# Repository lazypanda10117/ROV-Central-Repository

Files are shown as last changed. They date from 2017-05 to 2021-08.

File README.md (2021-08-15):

## ROV Central Repository

The central repository for 3 underwater Remotely Operated Vehicles (ROV) created for the MATE competition.
They were designed by 3 different engineering teams in AIS between 2015-2017. 
Details about the project and contributors can be found in the corresponding directory.

<br>

**First year of competition - 2015**:

Details of the ROV: [Seagle](Engineering%202015%20-%20Seagle/README.md)

<br>

**Second year of competition - 2016**:

Details of the ROV: [Aquila](Engineering%202016%20-%20Aquila/README.md)

<br>

**Third year of competition - 2017**:

Details of the ROV: [Aquila II](Engineering%202017%20-%20Aquila%20II/README.md)

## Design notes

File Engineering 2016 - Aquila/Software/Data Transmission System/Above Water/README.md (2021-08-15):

# Description of the code

We used the I2C protocol to get the raw data from the under water Arduino to the Arduino above water. Then, we process data and produce human readable information about the current state of the ROV.

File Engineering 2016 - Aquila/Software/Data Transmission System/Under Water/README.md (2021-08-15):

# Description of the code

<br>

**Pressure Sensor**:

The pressure sensor is a relatively small and delicate device, and thus, during the soldering process, it requires definite precision. The pressure sensors after soldering is then waterproofed so that it can be used under water with full exposure. Our system uses an I2C bus communication protocol to interact with the pressure sensor. The data retrieved from the sensor is in mBar (0.1 kilopascal). The main usage of the pressure sensor is to measure the depth of the ROV while under water. Our team has devised an equation for calculating depth based on standard results in fluid mechanics.

<br>

**Temperature Sensor**:

The temperature sensor we have chosen for our ROV is model DS18B20. We deliberately chose DS18B20 as our thermometer because it is waterproof and it uses a unique 1-Wire interface, which requires only one port for communication. The temperature sensor can accurately measures temperatures from –55°C to +125°C (–67°F to +257°F) with only ±0.5°C error.

<br>

**Transmission of data**:

These sensors' data will first be sent to the Arduino under water. Then, it is processed before being sent to the Arduino above water through a CAT-6 ethernet cable. These data will then be displayed on our computer in a custom application we developed using Processing.

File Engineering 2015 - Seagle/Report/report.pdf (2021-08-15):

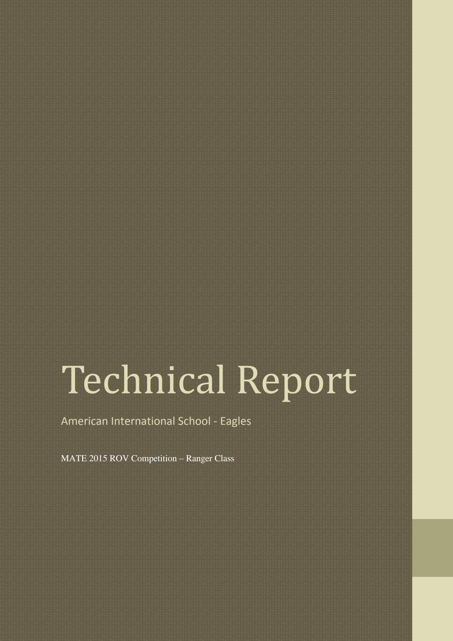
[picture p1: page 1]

# Technical Report

## American International School - Eagles

MATE 2015 ROV Competition – Ranger Class

# Table of Contents:

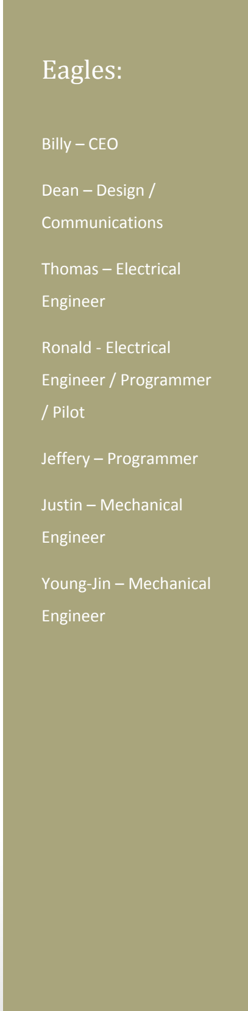
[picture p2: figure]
Technical Report; Eagles:; Billy – CEO; Dean – Design /; Communications; Thomas – Electrical; Engineer; Ronald - Electrical; Engineer / Programmer; / Pilot; Jeffery – Programmer; Justin – Mechanical; Young-Jin – Mechanical

- Introduction
- Rationale for Design:
- Frame
- Propulsion
- Positioning of Thrusters
- Human-Machine Interface
- Camera
- Teamwork
- Safety
- Reflection
- Future Improvements
- Troubleshooting
- Budget
- System Integration Diagram

# Introduction:

Eagles, a young, innovative company dedicated to sea exploration

technology, was formed on August 2014. Eagles is notable for its diligent

employees who worked late nights to engineer their first product – The Fried

Seagle. Its employees are the elites of American International School, who has

been selected through rigorous examinations. Members of the team work on what

they enjoy: coding the human-machine interface program, water-proofing wires,

assembling and positioning the components of ROV. Although seemingly branched

out, all members are knowledgeable and familiar with the product.

- Comment from CEO:

Dream team! Managing and overlooking production for this company is

barely needed. Our employees are knowledgeable, committed, and eager for the

completion of our products. What they do not know will lead their curiosity to

experiment or ask other employees. Eagles provides a welcoming-environment,

where employees are considered family and all opinions are heard and considered.

- Comments from Founder:

I am pleased at the progress our company has made in its first year. The

dedication and determination of our young engineers had been an inspiration to me.

I envision a bright future for this company as employees display their collective

drive and thirst for ocean exploration and technology.

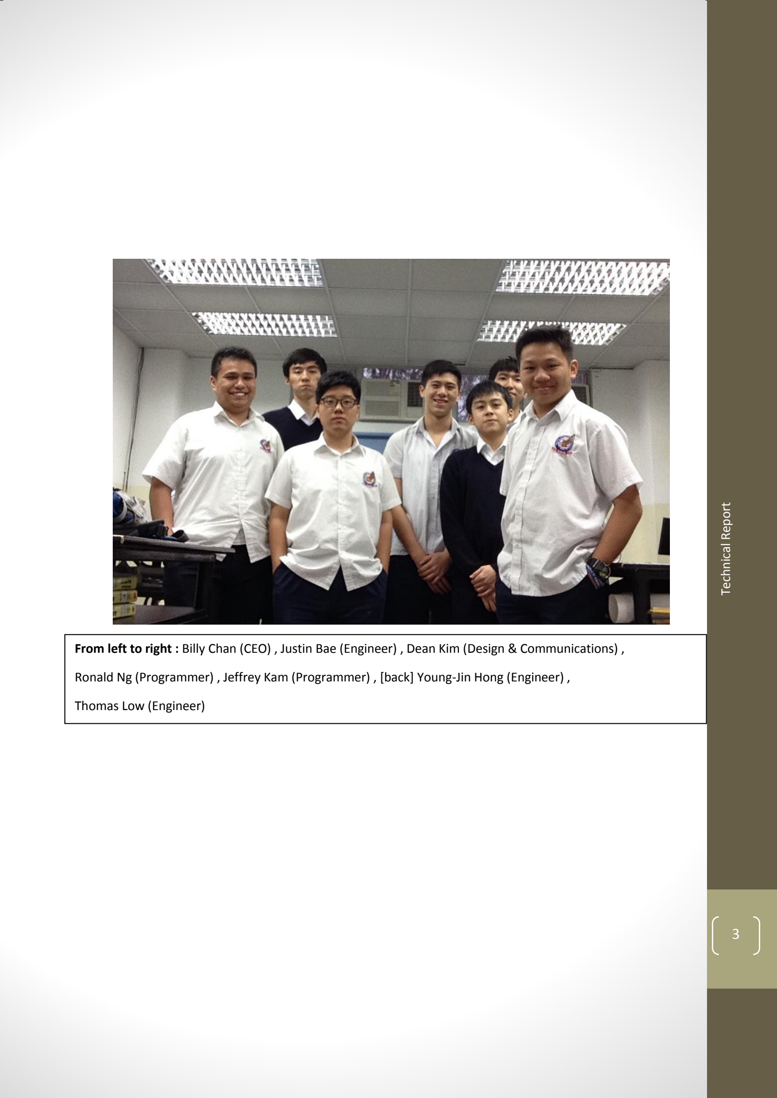
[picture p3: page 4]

Technical Report

3

From left to right : Billy Chan (CEO) , Justin Bae (Engineer) , Dean Kim (Design & Communications) ,

Ronald Ng (Programmer) , Jeffrey Kam (Programmer) , [back] Young-Jin Hong (Engineer) ,

Thomas Low (Engineer)

# Rationale for Design:

- Frame

A cubic frame design has been selected. PVC pipes and joints (L & T) are used

for this particular ROV. There are many advantages of using a PVC pipe. First

of all, the low cost of PVC is definitely and attractive aspect. The light weight

of PVC is another advantage since it ensures unrestrained movement and less

force is required to move the ROV. Durability is also achieved by the cubic

shape as there is no overall weak spot due to the symmetry of the shape. The

design allows easy modification: addition of parts such as lasers, sensors,

cameras, and storage units can be done easily. This model also leaves space

inside the ROV so larger components could be attached inside the cube and

remain protected from collision.

- Propulsion:

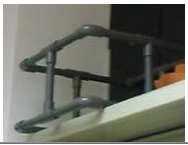
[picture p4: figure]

The ultimate aim for the propulsion system is to provide flexible

underwater movement to the ROV so that it could successfully accomplish

Cubic frame resting on a shelf

5

the missions with great efficiency. Our propulsion system involves six

motors to allow maneuverability in any direction. Motors are made from

bilge pumps, carbon-hydro propellers, and PVC pipes. The large-diameter

PVC pipe is used for shielding. Shielding the propeller is integral to the

performance of the propeller: not only has it prevented cavitation, but also

improved the power of the propeller by minimizing energy loss.

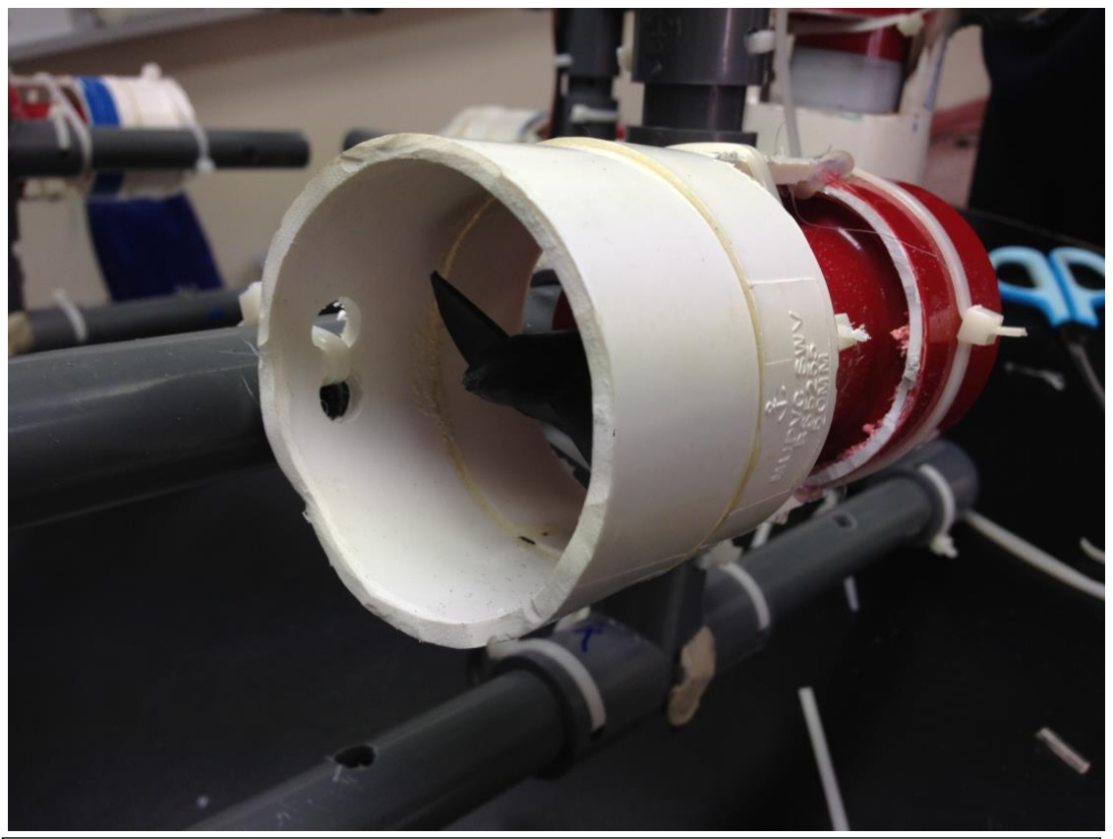
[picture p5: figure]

Positioning of Propulsion

To achieve balanced propulsion for The Fried Seagle, four horizontal

motors are placed symmetrically at each corner of the cubic frame,

relative to where the ROV is facing forward, all in different directions.

One of the motors of The Fried Seagle’s Propulsion system

This positioning allows shifting of the ROV in all horizontal directions

and even provide a vertical motion. Additionally, the positioning provides

a maximum torque when the ROV is performing rotation.

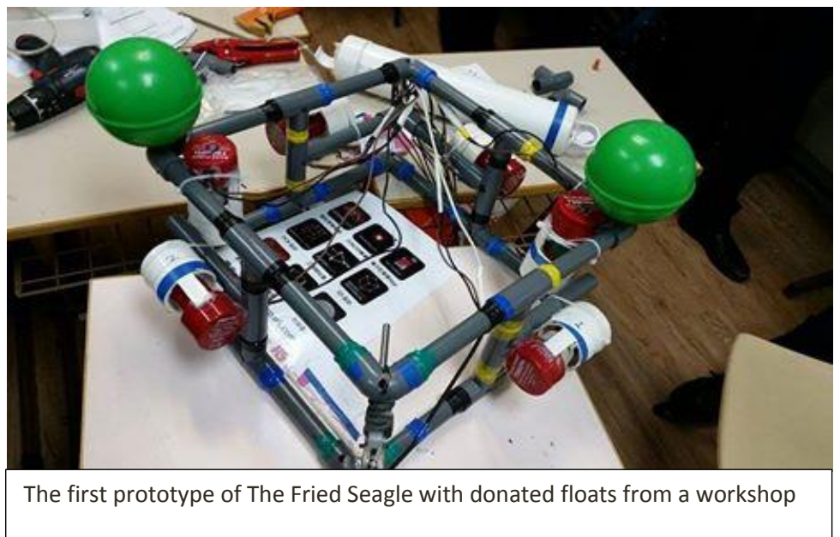
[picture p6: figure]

- Camera:

Seemingly simple to construct, camera plays a vital role in the functioning

of the ROV (after all, clear vision is a must-have for accomplishing any

mission).

The Fried Seagle is equipped with three cameras, frontal camera, down

camera, and full view camera.

- The front camera is the main camera as it shows what is in front of the

ROV. It would be used mainly during inspection missions.

- The down camera is used to identify objects that are under the ROV. As

the ROV is handling tasks underwater, materials might sink and fall to

The first prototype of The Fried Seagle with donated floats from a workshop

7

the bottom. Hence, a down camera could effectively aid in retrieving

any objects sank at the bottom using the hooks.

- Interestingly, the back camera is attached to the wires rather than the

ROV itself. Since it is located above the ROV, it provides a third

perspective to the ROV and hence it can view the surroundings better

and make correct judgements.

All the cameras are based off Spy-Hole B/W Camera K701. These camera

were chosen since they are slim and easily be customizable. Each camera

is inserted into an 11 cm long clear acrylic tube and linked to 5 meter long

cable (directed to a CCTV module, which displays on a portable

computer). It is waterproofing the camera determines the fate of the ROV.

To ensure perfect seal to prevent water from contacting camera and the

soldering inside the tube, 2-part epoxy is used.

- Human-Machine Interface – Programming

Swift Seagle is the program in which human interaction with The Fried Seagle is

made possible. Swift Seagle is composed of sophisticated arithmetic and logical

coding, allowing the Fried Seagle to maneuver at controlled speeds in 3 dimensions

with the input of a PlayStation 2 controller. The swift eagle uses the x and y values

to generate different speeds for each individual motor in order to move in curve

path through various speed. The analog stick of the PS2 controller returns a value

of its x and y value which are between 0 and 255. The way we code the swift eagle

is to think of the x and y values as coordinates, and divide the analog stick into 4

quadrants, like the Cartesian plane, with the x and y values of the analog stick at

stationary point as origin.

9

# Teamwork:

Our company entered the MATE ROV competition for the first time;

therefore, we did not have any experience of engineering a ROV. As we were

constructing the ROV and going through all the trial-and-error, we discovered that

teamwork is the most important aspect. Making this vehicle requires ample

knowledge from various fields: designing, fluid dynamics, mechanical engineering,

computer programming, and material engineering. The robot is the synergy of

those skills and signifies how these skills produce a harmonious spark in

technology. Ronald and Jeffery, who possessed talent and passion for computer

programming, worked on programming the motors. Justin, Young-Jin, Jack worked

on mechanical parts on ROV. Thomas provided us requisites for ROV, including

tools and materials for ROV frame and camera and worked on electrical parts for

ROV. Dean worked on technical report since he acquired an overall knowledge

about ROV. As a president of Engineering Club, Billy managed the team and

allocated our work efficiently and showed us great responsibility to this task. Unite,

we stand – Our team boasted one’s unparalleled strength and each member

contributed to the strenuous task of construction a ROV. We discussed with each

other and shared each other’s ideas. We would seek ways to improve and modify.

The fruit of the hard discussion was a collage of ingenious ideas weaved together.

Without doubt, teamwork was the MVP of our success in the first attempt to

construct an underwater ROV.

# Safety:

Safety of the ROV is one of our primary concerns when we were designing

the ROV. The Fried Seagle has been designed to meet the competition's safety

requirements. The team followed strict safety procedures during the engineering of

the ROV. We ensured that all electric parts must be sealed perfectly to eliminate

gap for water to leak in and cause a short circuit. During our construction of the

ROV, the crew must adhere safety procedures. We ensured that the proper safety

equipment are worn when using specific tools including saws and drill. Propeller

For instance, shields had been used to prevent people from accidents caused by the

blade of the propellers. Each engineer has received training on the correct use of

the tool that were used during construction and every one followed a strict safety

protocol to ensure the highest degree of safety.

11

# Reflection:

Considering the size of our team, insufficient manpower, and lack of time,

our engineering team has gained an ultimate success in completing a full-

functioning ROV. We understand the down-sides of our vehicle, Eagles is proud to

present The Fried Seagle as the first Engineering club at the American International

School, and to represent our great school against others. With flaws, we find

solutions, and with these solutions, we have learnt great lessons on how to deal in

situations. We are looking forward to further develop and burnish our lessons and

knowledge to culminate a more advanced, well-reflected vehicle.

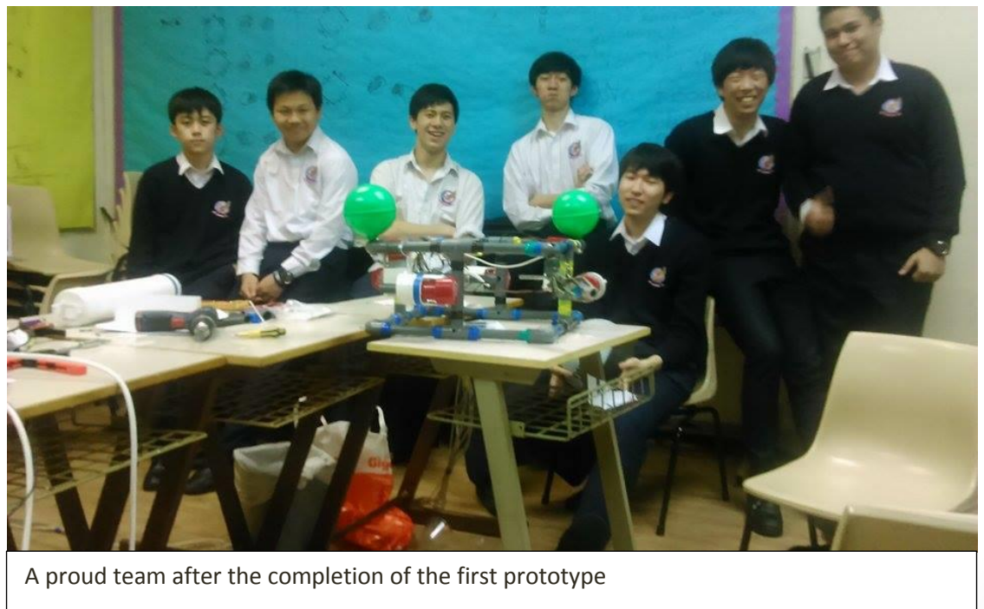
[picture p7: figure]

A proud team after the completion of the first prototype

# Future Improvements:

Since we were novice to constructing ROV, for the first 2 months, our team

worked inefficiently. Having obscure plans for constructing ROV, our club

members did not work efficiently and had to rearrange our frame design a

lot. Every procedure of constructing ROV was a new challenge that almost

everyone had not encountered before; as a result, we constructed our basic Frame

of ROV ineptly, causing re-work of our whole processes. We need to have clear

and detailed plan about ROV construction before we engage the construction. By

doing that we can save more time and consider about our mechanical and

mathematical parts of ROV. We need to calculate actual mechanical physics to

decide with backing proof that our decisions are the best ones. The team’s ambition,

excitement, and impulsiveness has produced a ROV that can and will be even

better.

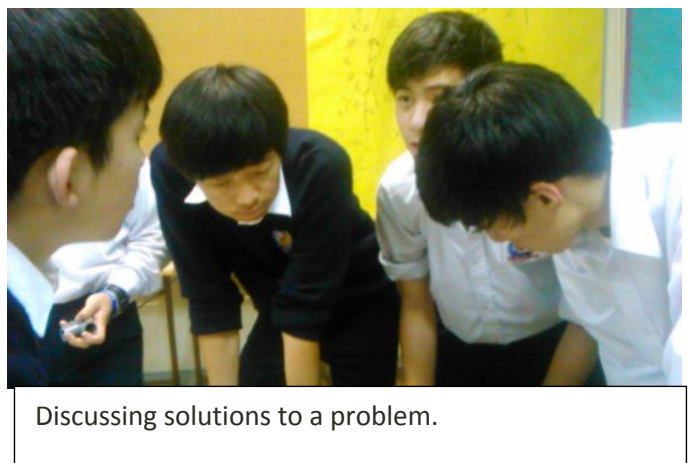
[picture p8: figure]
Discussing solutions to a problem.

13

# Troubleshooting Techniques:

For the efficiency of the work, our company had set up 2 protocols for

troubleshooting. One is used for programming components of the ROV, while the

other manages the mechanical components of the ROV:

- Programming

I

### •Debug the logic of the code by printing out all the output values

II

### - Print the value with a description of what this output means and chec k if it corresponds with the reality

### III

### - check if the pin is working properly

IV

### - draw diagrams on paper to make a thought experiment on how the wi re will be connected and how the code will be executed

V

### - Check the voltage and current passed to the pwm and the voltage and current needed for the motors

VI

### - If doesn’t detect ps2 controller, try adding a 2k resistor for the data wi

re.

# Budget:

As newly-born club, the Engineering Club does not receive a budget from

the school. However, the ambitious members would not allow such a chance to

pass away with the inability to attempt The MATE Competition merely due to a

financial situation.

Starting Budget (Donated from various members of the Eagles company): 3,000 HKD

Item | Quantity | Price per unit | Sub-Total
PVC pipe (2 cm diameter) | 3m | 20HKD/m | 60 HKD
PVC pipe (8.5 cm diameter) | 0.5m | | 10 HKD
PVC cap (for 8.5 cm diameter) | x2 | | 10 HKD
PVC joints (10 L-joints, 8 T-joints) | X18 | | 90 HKD
Two part epoxy | X2 | 270 HKD/set | 540 HKD
Speaker wire | 50m | 30 HKD/5.7m | 263 HKD
Video wire | 12m | 3.5 HKD/0.3m | 140 HKD
Camera | X2 | 280 HKD/unit | 560 HKD
Already water prepared camera | X1 | | DONATED
PWM | X6 | 90 HKD/unit | 540 HKD
Arduino Mega | X1 | 220 HKD/unit | 220 HKD
Arduino Leonardo | X1 | | DONATED
Plastic enclosure | X1 | 75 HKD/unit | 75 HKD
Cable Wire | X3 | 30 HKD/pack | 90 HKD
Sony PlayStation 2 Controller | X1 | 80 HKD/unit | 80 HKD

15

Heat Shrink | ?? | | ~30 HKD
CCTV module | X1 | 398 HKD/unit | 398 HKD
CCTV module-video wire adapter | X4 | 40 HKD/unit | 160 HKD
Male to Male video wire | X4 | 18 HKD/unit | 72 HKD
800GPH Bilge Pump | X3 | 280 HKD/unit | 840 HKD
750GPH Bilge Pump | X3 | | DONATED
Food for workshop | X3 sessions | ~20 HKD/person | ~80 HKD
Tools (Wire stripper, solder, scissors, etc.) | X6 | | 360 HKD

ROV net Total : 2,793 HKD

# System-Integration Diagram: Water

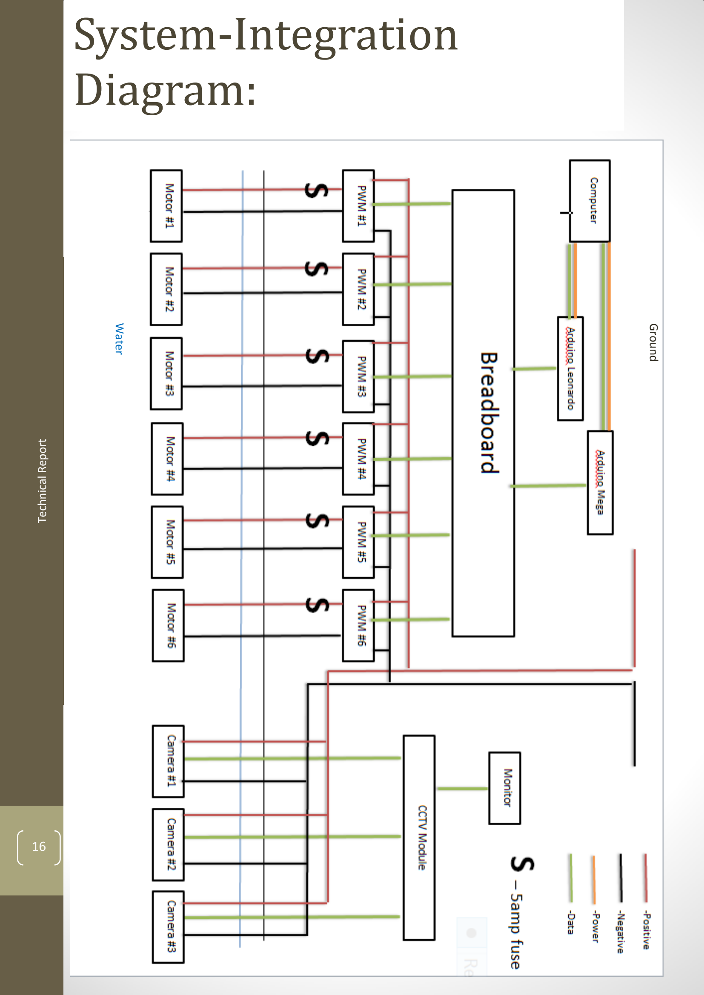
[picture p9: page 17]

Technical Report

16

Ground

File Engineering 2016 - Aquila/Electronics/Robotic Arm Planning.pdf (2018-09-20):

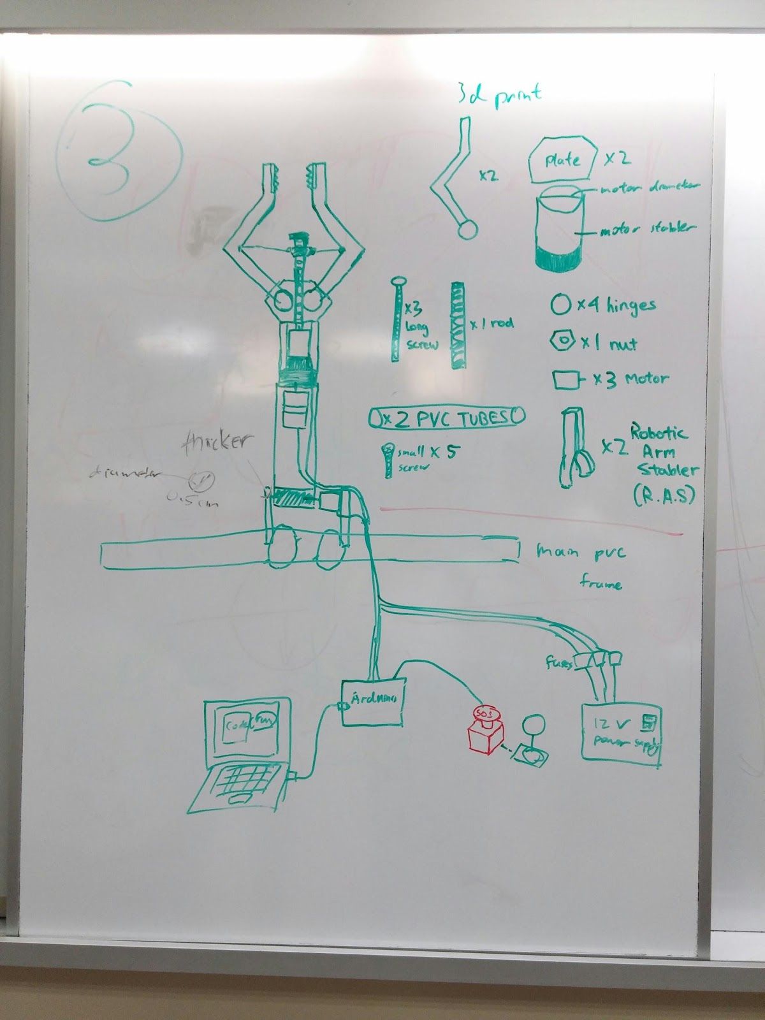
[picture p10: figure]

3D printed parts:
Arm base round as diameter of motor below with 4 hole near the edge and with a distance of the thickness of the jaws on opposite side and a hole in its center
Motor holder, round with a bit larger than the diameter of motor and height of the whole motor + 5 cm

Robotic arm stabler
A small rectangle solid 1.2x3.0 cm with 2 exerted holes on 2 side for insertion of 2 nail
2 square sticks with holes on their ends slightly bigger than the nail size
2 jaws with 2 holes in the end to insert the rod for pivot
2 small rod with diameter of 1 cm with holes on 2 near end with a distance of the thickness of the arm plus the diameter of the screw.
Another motor holder with length of motor length times 2 and cross sectional area of motor diameter + 2 cm and with a 3 cm solid base for inserting a high torque motor to rotate the arm
A round place with 0.5 cm thickness and diameter of previous motor holder and also a little hole in the middle

*all motor holders have 0.5 cm thickness

Non 3d printed parts
6 Brass or bearing
One motor with really high torque
1 motor with medium torque
1 servo
2 plastic soft frictional thing

4 nut for arm linear motion hinge
4 small screw for the hinge also

8 nuts for additional height above the arm base
4 medium long screw
4 nuts for stabling the pivot rod for the jaws

4 screws for connecting the motor holder and arm base

Epoxy glue
3 meter wires
Wire Connecter
2 pwm for 2 motors
Lots of Arduino wires
1 bread board
1 arduino mega or 2 arduino uno
A 4 way joystick
bIg RED BUTTON

http://www.robotoid.com/howto/choosing-a-motor-type.html

Waterproof DC Motor:
http://letsmakerobots.com/content/waterproofing-dc-motor-sugruhttps://www.youtube.com/watch?v=wIcCz5m9LwQ

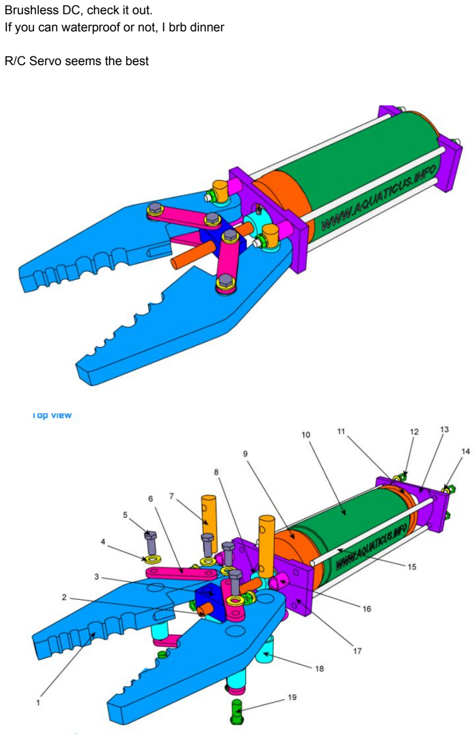
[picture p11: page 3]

Brushless DC, check it out.
If you can waterproof or not, I brb dinner

R/C Servo seems the best

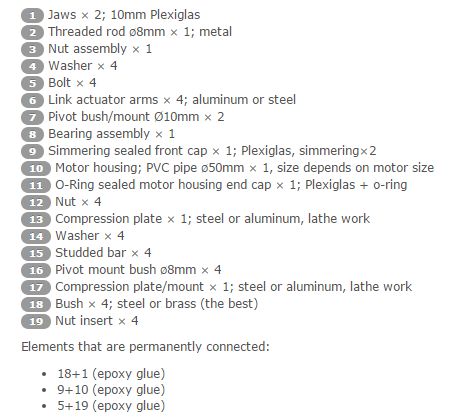
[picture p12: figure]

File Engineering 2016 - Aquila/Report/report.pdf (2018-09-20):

# AQUILA INTEGRADED SOLUTIONS

# american international school hong kong , hong kong

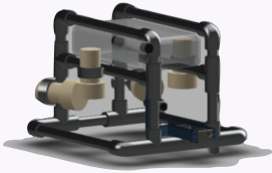
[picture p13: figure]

Billy Chan, Class of 2016
Chief Executive Officer &
Founder

Thomas Low, Class of 2016
Chief of Electrical Engineering

Ronald Ng, Class of 2017
Electrical Engineering

Jamie Fox, Class of 2019
Head of Technical Writing

Tim Chen, Class of 2019
Engineer

Justin Lee, Class of 2019
Engineer

Justin Bae, Class of 2016
Chief of Mechanical Engineering , Project Manger

Jeffery Kam, Class of 2017
Electrical Engineering

Megan So, Class of 2019
Communications Director

Michael Chan, Class of 2019 Engineer

Tony Kovari, Class of 2019 Engineer

Justin Cheung, Class of 2019 Engineer

## The Aquila

### TABLE OF CONTENTS

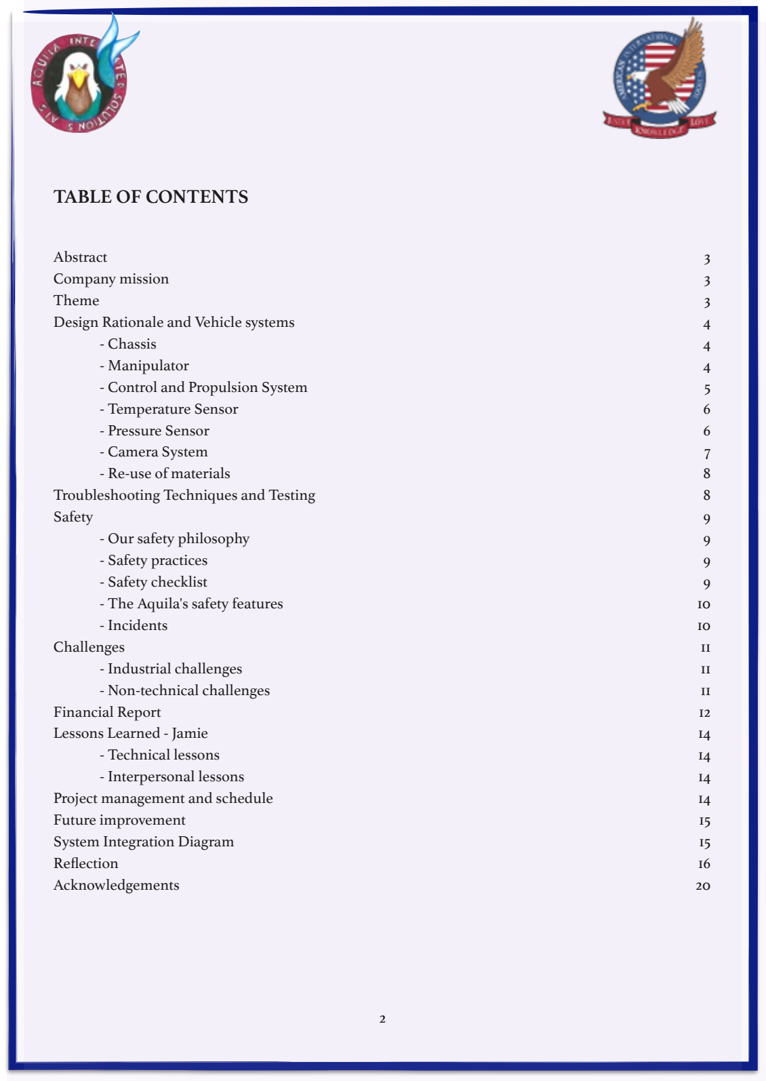
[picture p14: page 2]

Abstract
Company mission
Theme
Design Rationale and Vehicle systems
- Chassis
- Manipulator
- Control and Propulsion System
- Temperature Sensor
- Pressure Sensor
- Camera System
- Re-use of materials
Troubleshooting Techniques and Testing Safety
- Our safety philosophy
- Safety practices
- Safety checklist
- The Aquila's safety features
- Incidents
Challenges
- Industrial challenges
- Non-technical challenges Financial Report
Lessons Learned - Jamie
- Technical lessons
- Interpersonal lessons
Project management and schedule Future improvement
System Integration Diagram Reflection
Acknowledgements

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
Aquila Integrated Systems (AIS) is proud to present its flagship remotely operated vehicle (ROV) product, Aquila. Previously known as Eagles, with new recruits and experience to base our work off of, it was only fitting that the company underwent a name change. From the ashes of The Fried Eagle rises the versatile Aquila. The talented individuals at Aquila Integrated Systems have devised a ROV that is adaptable to the situation presented, adjusting individual modules of the ROV according environmental challenges. Aquila will be equipped with four bilge pump motors (each with propellor shielding), four waterproof cameras, a temperature sensor, a water pressure sensor, and a rotatable mechanical arm. Thanks to the modular design, the company is able to have several mission-critical components created at the same time. With the team coordination from team leader Justin Bae, each module of Aquila does not interfere with another. With its affordability, fixability, and most importantly–adaptivity, Aquila is the ideal ROV for astronautical customers with intent on exploring the depths of oceans in far away worlds.

### ABSTRACT

Aquila Integrated Systems offers practical options through application of different fields of science. This year’s product embodies these fields with our specialized members in mechanical engineering, electrical engineering computer science, and even astronomy (specialized members are enthusiastic or have planned to study in these respective fields when they enter college). AIS seeks innovative solutions to produce awe-inspiring systems with state-of-the-art functionality for our clients.

### COMPANY MISSION

For a company that emerged out of the American International School, it seemed only fitting that the competing ROV team’s name matched the school-wide Eagle theme. The Aquila has an astro-marine focus with the features for effective marine exploration and accessibility and flexibility for the various challenges in space.

### THEME

CHASSIS
The objective design of the chassis was to reduce the amount of material used so that it is easier to control in terms of buoyancy. We decided to use PVC pipes to construct the fundamental shape of the ROV, as we are able to manipulate it very easily and it is strong enough to hold the components of the ROV, but soft enough for us to cut. This gives us a lot of flexibility in terms of changing the dimensions of the ROV. We also drilled holes into the ROV, as it allows the entire chassis to sink. This also makes the buoyancy easier to control and would increase the manoeuvrability of the ROV. We decided to make the Chassis shaped like an upside down pi so that we can input storage space for the ROV’s non-waterproof components. Our design is very minimalistic, as it helps us find any mistakes or broken parts on the ROV very easily. We used PVC pipe glue to secure the parts, as it prevents unnecessary imbalances to how much water is in the chassis. This method is to also add minimum amount of weight to the ROV, making it easier for us to control.

### DESIGN RATIONALE & VEHICLE SYSTEMS

MANIPULATOR
Aquila’s manipulator uses two servo motors; one for opening and closing the jaw, and one for rotation the grip. Since the servos are attached directly to the rotating part, the grip is very durable and free of minor mechanical faults.

Another noteworthy feature of Aquila’s manipulator is that its body is built out of individual aluminium blocks. Hence, we did not have to rely on certain predetermined configuration but were able to easily design and construct the manipulator frame that suits our purposes: First, by using the blocks, we were able to create and attach a platform for the camera on Aquila’s manipulator body. In fact, versatile nature of the blocks allowed us to attach the platform at the ideal location we want. Also, by attaching a PVC pipe joint of the main frame to the manipulator body, we ensured that the manipulator be attached rigidly and naturally to the frame.

CONTROL AND PROPULSION SYSTEM
The control system has a dramatic change from last year’s PS2 design. The control input system includes a Thrustmaster joystick, 2 buttons for up and down movement, and 4 buttons for metallic grip movement; The brain of the control system is 3 arduinos (2 uno and 1 nano); The control output system includes 4 pwm controlling 4 separate motors. The fundamental concept of how the joystick controls the ROV is that the system’s code convert the analog values retrieved from the joystick to x and y values based on the joystick’s center location. Since the analog values received from the joystick are too unstable due to the joystick's sensitivity, the system accounts for the constant varying data first by limiting the maximum and minimum values and then by dividing the each joystick axis into 21 sections, 10 above and to the left of the midpoint section, 10 below and to the right, and one for the equilibrium point. Our team achieve this by mapping the analog value in the constrained range (around 120 to 940) from -10 to 10, and setting 0 as the equilibrium point.

Unlike last year, the xy value is not combining to create a cartesian plane, instead, it separates x as the rotation factor, and y as the linear propulsion factor. For the rotation factor, the system will rotate the ROV in the relative direction of the center of joystick with a speed proportional to the magnitude of the joystick movement. For linear propulsion factor, the ROV will propulse in the y direction of the joystick; simply put, if the joystick location is above half, then it moves forward with magnitude respective to the difference from center, and vice versa for backward. To make the transition from linear propulsion state to rotation state, our team have installed a button that when it is pushed, the system will change to the rotation state and when released, it will return back to linear propulsion state as default. For the z motion (up and down motion), there will be 2 seperate button exclusively for that control as the joystick only provides 2 variables. Our system does not take speed into account for the up and down motion, because usually up and down motion is not a continuous task and does not require as much precisions compared to x and y motion.

The hardware design of the system separates mainly into 2 groups, one for controlling movement, which will be an isolated system that process all the computation above water, and the other for receiving sensors’ data underwater and controlling the arm movement, which transfer data back and forth between an arduino above water and one underwater. There will be 2 different programs in the system, one for reading the joystick analog input and 2 buttons input to control the main ROV movement, and the other for transfer data such as temperature and pressure from the one underwater to the one above water and transfer arm movement input to the one underwater to perform arm motion. The arm itself has 2 servos, one for opening and closing the metallic grip, the other for rotating the whole grip. The second servo is installed due to specific mission. Each servo will have 2 respectives button for controlling, one for each direction for the servo to move. The system also has a safety mechanism that will keep track of the position of the servo so it wouldn't reach the maximum of the degree it can turn and break the servo internally.

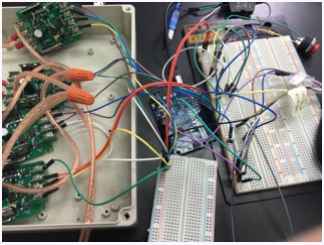
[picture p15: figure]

CAMERA SYSTEM
The Aquila is equipped with four cameras, frontal camera, down camera, and full view camera. The frontal camera is used during missions in inspection missions, and allowing. It also gives use an idea of where we are going. The camera on the arm provides a precise view on the action of the arm, allowing the action to be more precise and making it easier to complete the objective. The down camera is used to help us in locating the object underneath in order to complete the missions, and to locate things that are underneath the ROV. This would help us in obtaining the objects from below. The full view camera is used to provide a birds eye view to the whole pool which allows us to know where everything is in order to plan how to go to each places.

All our cameras are made with Spy-Hole B/W Camera K701. We chose this camera mainly because it is small and easier to be customized. Each camera is put inside a11 cm long clear acrylic tube, linked to 15 meter long cable which is directed to a CCTV module into a computer. We used a 2 part epoxy to seal the camera inside. The reason we chose to use acrylic tube is because it is strong enough to withstand the water pressure, rather than a plastic bottle. Epoxy has the ability to leave no gaps for water to go through into the camera.

The camera systems's power are connected to 4 Underwater Camera Interface circuits. These circuits are capable of transforming 20-9 volts of electricity to 5volts, which the cameras runs on. The circuits consist of one 50v 100μF capacitor, 35v 0.1μF capacitor and a LM7805 voltage regulator. The capacitors are used to prevent damages from the short circuit while the voltage regulator is used to decrease the voltage to 5 volts in order for the camera to use. The circuit is based on a perfboard as it is a lot more flexible during maintenance and debugging. All of the power circuits are enclosed inside a waterproof enclosure with several outlet so that it is completely detachable from the ROV.

Control System Prototype

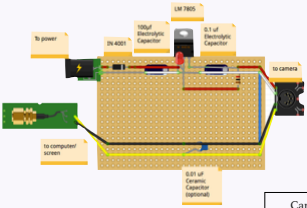
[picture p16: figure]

Camera circuit design

PRESSURE SENSOR
The pressure sensor is a relatively small and delicate device, and thus, during the soldering process, it requires definite precision. The pressure sensors after soldering is then waterproofed so that it can used underwater with full exposure. Our system uses I2C bus communication to interact with the pressure sensors and the data retrieved from the sensors is in mBar, in other words, 0.1 kilopascal. The main usage of the pressure sensor is to measure the depth of the ROV underwater. Our team has devised an equation (int)((pressure*100*1000)-101325)/(0.993*9.8) for calculating depth based on the equation pgh in fluid mechanics. The design of the system is that the pressure sensor will send data to the arduino underwater, then the data is processed into depth through the equation above and then send to the arduino above water through ethernet wire and softwareSerial protocol. The data will then display on the computer's monitor through an application we wrote in Processing, which reads the serial output of the data and display in an organized form on the screen.

TEMPERATURE SENSOR
The temperature sensor we have chosen for our ROV is model DS18B20. We deliberately chose DS18B20 as our thermometer as it’s waterproof and it uses a Unique 1-Wire interface which requires only one port pin for communication. Our temperature sensor can accurately measures temperatures from – 55°C to +125°C (–67°F to +257°F) with only ±0.5°C error.

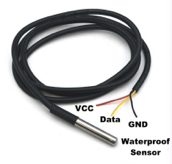
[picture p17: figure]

Diagram of sensor

RE-USE OF MATERIALS
Aquila Integrated Systems salvages and re-uses previous products (The Fried Eagle) solely for tests. With the upbringing of new and sometimes unconventional ideas, it is a certainty that members will have failed to account for errors, even after validation of the new system’s and calculations. Prioritizing safety of the members, re-used materials such as motors, floats, and PWM have been worn-out, experienced leakage, and overheated to the point of flame ignition (respectively). This use of the obsolete items ensures complete development of our solutions, having tested and accounted for all factors (particularly any extraneous aspects that may affect operational performance), as well as test reliability of the system.

All materials that make the Aquila were never of The Fried Eagle. Parts with improved specifications are required for our company’s progressing advancement of our solutions, thus our annual acquisition of brand-new materials is a testament to the company’s growth.

### TROUBLESHOOTING TECHNIQUES AND TESTING

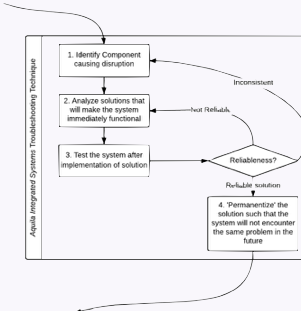
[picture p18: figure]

Safety Philosophy
Safety in using the ROV is one of our primary concern when we were designing the ROV. The Aquila has been designed to meet the competition's safety requirements. No safety issue is too small for us. We employ this philosophy to our design and working habit. After multiple check and test, we have determined that our product meets all the safety standards of IET.

### SAFETY

Safety Practices
The team follows strict safety procedures when the ROV is being constructed. We ensured that all electric parts cannot not have any gap for water to leak in and cause a short circuit. During our construction of the ROV, the crew must follow safety procedures. We ensured that the proper safety equipments are worn when using specific tools including saws and drill. Each engineer has received training on the correct use of the tool that were used during construction and every one followed a

Safety Check

Safety Checklist at Work | Check

Long Hair is tied back

Gloves are worn when handling eproxy

Hearing protection and safety goggles are worn when operating power tools and motor circuits

Clear workstation completely after work

Unplug soldering iron after use

Never touch the metal section of the soldering iron, regardless circumstances

Safety Checklist before Operating the Aquila | Check

All wires are securely connected to ROV

Both ends of the tether are properly lugged in.

Run system check (include motors, cameras sensors)

ROV is securely connected to 12V DC battery.

Safety Checklist when Operating the Aquila | Check

All staff around the pool are aware of the deployment off the ROV

Only one member can act as pilot

No member is allowed to touch the water pool when ROV is in operation.

The Aquila's Safety Features
- Motor Shields has been used to prevent people from accidents caused by the blade of the propellers.
- The tether is tightly secured
- All sharp edges smoothened.
- 25A fuse on main power source.
- Each motor is fitted with a 5A fuse.
- The ROV is also designed to be light which would reduce the force and momentum during a collusion.
- Labels are tagged on wires to prevent users to connect device in the wrong polarity.
- yellow and black safety warning color indicators on motors and other hazardous items
- One camera is tied to the tether for full view of the ROV and its surroundings.

Incidents
Despite the fact that we have taken every single safety, there were still several incident during the development of our ROV. One of notable incident during the development of the ROV took place during the production of the motor control. The PWM circuit for our motor caught on fire during use. We have replaced the PWM circuits with a different model and we included wearing safety protection as one of the protocols when operating the motor circuits just in case. There was another incident when one of our member's hand was injured by a hot soldering iron. After this incident, we especially designed to items on the checklist concerning soldering irons to decrease the possibility of similar accident.

NON-TECHNICAL CHALLENGES
As a novice team, the main problems of the team stemmed from the fact that majority of the teammates were new to the team. Our progress was therefore often heavily reliant to few senior members and resulted in inefficient teamwork

Failing to sufficiently familiarize new members to our project also led to overall lack of motivation. Since many of the members were not fully aware of the necessary concepts or skills, their participation was often very limited.

Lack of organization was also a huge problem that emerged in this context. At the beginning, our team divided ourselves to several sub groups and assigned different tasks to each group. However, as each groups began to encounter more and more problems, the independent nature of each groups resulted in inefficient troubleshooting process that had to be coped only within the group.

### CHALLENGES

TECHNICAL CHALLENGES

One of the main sources of our technical problems came from the Arduino. Failing to accurately wiring the PWM boards and the motors often burnt the Arduino, and members had to make unplanned expenditure in purchasing new sets of Arduino. After several trial and errors, we were finally able to solidify the connections.
Using a joystick to control the motors entailed several problems as well. First, the Arduino code didn’t receive any signal from the joystick if the joystick lever was not tilted perfectly toward 90 degrees angle. This problem prevented us from manipulating the vehicle swiftly and smoothly, since it was it was impossible for us to tilt the lever toward precise right angles continuously.

Unwanted penetration of liquid was another major hindrance. First of all, careless waterproofing often led to fault in our cameras, buoyancy, and especially the robotic arm (the Arduino and other electric boards for the arm are enclosed in the watertight case that submerges underwater with the vehicle).

Budget and Expense Sheet

TYPE | ITEM | UNITS PURCHASED | UNIT PRICE (HKD) | UNIT PRICE (USD) | AMOUNT PRICE (USD)
Frame Section | PVC Pipe (2 metres) | One | $89 .00 | $11.47 | $11.47
Frame Section | Buoyancy Toilet Float | Two | $5.00 | $0.64 | $1.28
Frame Section | Watertight Electronics Enclosure | One | $299.00 | $38.54 | $38.54
Frame Section | PVC Glue | One | $5.00 | $0.64 | $0.64
Propulsion | Blige Pump Motors | Four | $150.00 | $19.34 | $77.36
Propulsion | Propeller | Four | $40.00 | $5.16 | $20.64
Propulsion | Propeller Adapter | Four | $80.00 | $10.31 | $41.24
Propulsion | Propeller Shield* | One | $49.50 | $6.38 | $6.38
Control System | Arduino Nano | Two | $89.00 | $11.47 | $22.94
Control System | Arduino Uno | One | $125.00 | $16.11 | $16.11
Control System | Joystick | One | $265.00 | $34.16 | $34.16
Camera | Rear View Camera (Automobile)* | Four | $206.00 | $26.55 | $79.65
Camera | Power Supply Circuit | Four | $35.00 | $4.51 | $18.04
Camera | Camera Circuit Enclosure | One | $110.00 | $14.18 | $14.18
Camera | Underwater Cable for Camera System | One | $158.00 | $20.37 | $20.37
Camera | Analog to Digital Video Signal Converter | One | $200.00 | $25.78 | $25.78
Camera | Four Channel CCTV Splitter | One | $497.00 | $64.07 | $64.07
Sensor | Digital Temperature Sensor | One | $35.00 | $4.51 | $4.51
Sensor | Pressure Sensor | One | $235.00 | $30.29 | $30.29
Sensor | Underwater Cable for Sensor System | One | $200.00 | $25.78 | $25.78
Arm | Servos | One | $241.00 | $31.07 | $31.07
Arm | Mechanical Claw | One | $123.00 | $15.86 | $15.86
Tools & Equipment | Drenal Drill | One | $1099.00 | $141.67 | $141.67
Tools & Equipment | Water Tank | One | $200.00 | $25.78 | $25.78
Tools & Equipment | Tool Box | Two | $150.00 | $19.34 | $38.68

### FINANCIAL REPORT

* signifies a donation

Expense | Amount in HKD Amount in USD
Frame Section | $402.70 | $51.93
Propulsion | $1129.20 | $145.62
Control System | $567.70 | $73.21
Camera | $1722.10 | $222.10
Sensor | $469.80 | $60.58
Arm | $363.90 | $46.93
Tools and Equipment | $1598.4 | $206.13
Travel Expenses | $300.00 | $38.69

### FINANCIAL REPORT

Total Cost: | $6,553.80 HKD | $845.19 USD

TECHNICAL LESSONS
Learning from our challenges and mistakes while building the Aquila, we have learnt to always have extra arduino boards incase of incidents where the arduino is burnt or is failing to work. Junior members have learnt our team leaders how to code, work the sensors, and developing the design. We have also developed a stronger, more efficient design that been developed by learning from our mistakes in the previous year’s design.

### LESSONS LEARNED

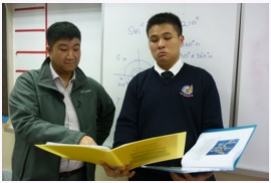
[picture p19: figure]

Mr. Kang and Billy Chan working on concept of ROV

### LESSONS LEARNED

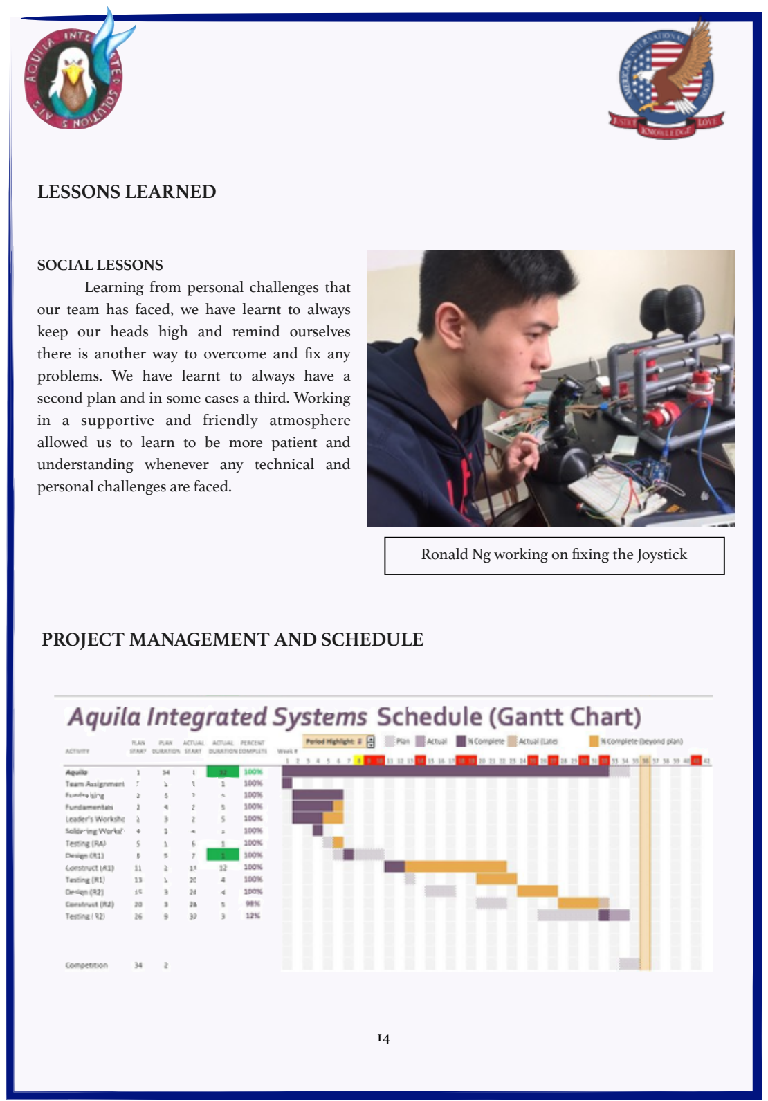
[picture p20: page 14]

SOCIAL LESSONS
Learning from personal challenges that our team has faced, we have learnt to always keep our heads high and remind ourselves there is another way to overcome and fix any problems. We have learnt to always have a second plan and in some cases a third. Working in a supportive and friendly atmosphere allowed us to learn to be more patient and understanding whenever any technical and personal challenges are faced.

### PROJECT MANAGEMENT AND SCHEDULE

Ronald Ng working on fixing the Joystick

Two major areas that need improvements for our team are the following: Lack of passion and Lack of sessions. First of all, due to general incompetence of the members, our teammates frequently experienced limitation to their participation, which eventually led to low motivation. This unpleasant cycle went on and on and lingered as a main source of general inefficiency and low productivity. Starting next year, with more passion and enthusiasm, we believe that our members will be able to participate to their full potential and reach fruitful outcome with our Aquila. In regards to this fact, it is imperative that our members first become competent engineers and gain sufficient knowledge and skill to participate. The problem of this year was that lack of available sessions hindered the progress of our learning. Hence, in order to boost up the passion of the members in the future and expect improvements, Aquila’s crews must first acquire sufficient time to hone their skills and contribute to their full potential.

### FUTURE IMPROVEMENTS

### SYSTEM INTEGERATION DIAGRAM

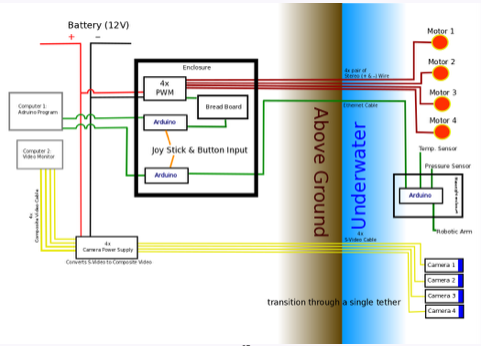
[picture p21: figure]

### REFLECTIONS

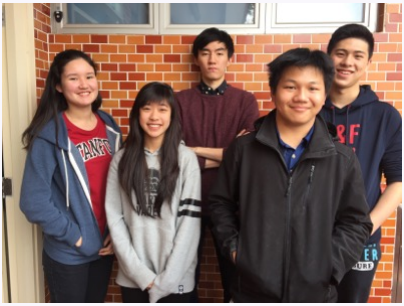
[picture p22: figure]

Justin Bae, Class of 2016
Although our team gathered and prepared for this competition as members of mere school extracurricular club, for me, it was a great opportunity to participate in an activity that I genuinely enjoyed. This competition gave me other several benefits. First of all, my experiences served as an excellent opportunity for me to apply the academic concepts, especially in Physics and Computer Science. By applying into tangible situations and objects, I was able to understand the concepts more clearly and easily, by which I even found chance to achieve pleasant outcomes for my academic endeavors as well. Also, as a team leader, my efforts in the club even allowed me to find opportunity to strengthen my capacity as a leader, through teamwork, resolving conflicts, and organizing the community. In the end, I regard my experiences preparing for this competition as a huge boon throughout my high school years and hope my fellow teammates to find pleasant benefits from this experience as well.

Members of ROV Team
Back Row (left to right): Jamie Fox, Justin Bae, Ronald Ng Front Row (left to right): Megan So, Thomas Low Missing Members: Tony Kovari, Justin Lee, Justin Cheung, Tim Chen, Jeffery Kam

Thomas Low, Class of 2016

This year is the second year I participate in the project. It is a great pleasure work with some old teammates. It is also great to see some new members participating in this project. As I am already familiar with the project I have helped my teammates to start training the new members in advance. I am currently leading the team of freshmen to build the camera system. I particularly enjoy the process of debugging the circuits. I am glad that I am able to use my knowledge from physics and maths to this project. By doing actual application, I am able to understand the subject more. Leading a team of freshmen also helped me on my communication and leadership skills. My experience working in this project has been a great part of my high school life, and I hope my teammates are benefit by this project the same way as I did.

### REFLECTIONS

Jeffrey Kam, Class of 2017

The two core values of engineering for me are exploration and problem solving. During the course of the ROV making process, I have enriched myself in those 2 values. I always try to explore new and more efficient solutions to the existing system, trying to improve it with better code and higher efficiency design. For example, from researching online, I realized that ethernet wire at CAT6 has really low resistance, and thus useful for our design for transferring data between underwater and on ground arduinos. This year, I also have to teach some of the freshmen how to integrate hardware into arduino and write a program that works perfectly uninspected. This new experience allows me to be a better communicator as i always keeps the idea and thinking process to myself and often explain concepts in an overcomplicated way. As one of the main programmer and electronics engineer in the club, I wish train some of the members on the team to have individual problem solving abilities and the heart to explore so in the future after i left, those will be able to make the team thrive with their ability to problem solve and guide the team to explore for new solutions.

Tony Kovari, Class of 2019

This is the first year I worked on any ROV and I learned a lot from the experience juniors and seniors in our team. We are very fortunate to have a great team leader that can motivate people to work and allow time for new members to get a look and feel of the work process. The designs and code made by our senior members benefited the team greatly, without them perhaps we would be behind schedule more than last year.

Tim Chen , Class of 2019

This is my first year in high school and the ROV team, so there were and still are a lot of things I don’t know. But throughout this year, I have learnt more and more on engineering in general from the seniors and juniors in the team. I am currently working on the pressure sensor with a fellow freshman; it isn't an easy job for us since we had no experience with engineering or arduino coding. But with the help from our teacher Mr Kang and other seniors/juniors, we had successfully made a working underwater pressure sensor. During this experience, I had enhanced my problem solving skills as well as my cooperation skills. I look forward to learn more and do more to help our ROV team in the future.

Michael Chan, Class of 2019

During the course of this club, i have learnt a lot about engineering. This was my exposure to engineering, so I had no knowledge that I can apply to this club. I have learnt a lot about arduino and also where to get tools to use. One major contribution I gave was the temperature sensor. First, we had to make sure the sensor was waterproofed. Then, we had to overcome a lot of bugs that prevented the code from working. After successfully running the code, it still did not show the temperature. With the help of seniors, juniors and the teacher, I have successfully made my first working physical product along with a working code.

Justin Lee, Class of 2019

After almost a year of being in engineering club, I have learnt a lot about engineering in general. This club was my first approach to learn about engineering. Throughout this year, I have learned how a ROV works and the safety precautions we have to take while engineering. My contribution to this ROV is working on the temperature sensor. With the help of a very advanced programmer and a teacher, I have successfully made a working temperature sensor with another freshman who also had no experience in programming programming. I look forward to seeing what I will able to accomplish next year with the knowledge I have.

### REFLECTIONS

### REFLECTIONS

Jamie Fox, Class of 2019

As a freshman in High School this year, I had set a goal to myself this year to learn and experience a range of clubs and teams that would help broaden my learning experience. I decided to join the ROV team as it seemed every different and interesting to learn about. Although I was a newcomer and did not know much about how to build an ROV, the senior members were very welcoming and patient. I have learnt so much from being apart of this amazing journey from attending workshops, making the cameras waterproof, and also designing this report. This has truly been a wonderful experience and I am very excited to continue this project.

Megan So, Class of 2019
As a student attending AIS, the engineering club is one of the only non-athletic clubs that stood out to me. This being my first year at the AIS engineering club, I thought it was a very enlightening experience and experiences are the best teachers for everything. I had no knowledge joining the club and through the club, I learned new skills, for example assisting and waterproofing the cameras. Not only was I able to learn new things, but I was also able to meet great new people. Our club was charmed to have an amazing teacher, Mr.Kang, who guided us through our difficulties alongside Bill, our club’s senior president.

Ronald Ng, Class of 2017
In these two years working on this project, I’ve encountered various challenges, learned different variety of things and met different people. The first year we join this competition, our team was compact, and had similar idea; it was really smooth working with them. This year, our team grew exponentially, many new members joined coming up from middle school, each and every excited for learning new things about engineering. As a senior member of this club, I was lucky to be able to teach the new members of the club about experiences that I’ve learned last year. Joining this competition inspired me a lot, I was surprised that we don’t even know majority of the world we live in because there’s still so much that we still haven’t discovered in the ocean yet. Also, I was greatly enriched with the problem solving skills I learned by joining this competition, the critical thinking and the team communication was something that I really enjoyed while working on the ROV. I hope to spread the knowledge and the fun of engineering to more students in the future.

### ACKNOWLEDGEMENTS

Aquila Integrated Solutions would like to thank and appreciate all the donations and sponsorships we have received. We couldn’t have accomplished the Aquila without our wonderful sponsors. Thank to MATE/IET for providing us the chance to compete and develop our critical thinking skills along the way. We also appreciate the American International School for providing us the space and sponsorship for the Aquila. Also, we would like to thank the donations that were donated from the inspiration night our company hosted to raise money for our projects that need funding. The inspiration night helped fundraise over $3000 HKD / $386.88USD. Lastly I would like to thank our teacher and team supporter Mr. Eunsup Kang. He has spent mass amounts of time helping and guiding us to where we are now.

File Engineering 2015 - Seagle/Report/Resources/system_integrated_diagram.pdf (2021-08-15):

## S – 5amp fuse

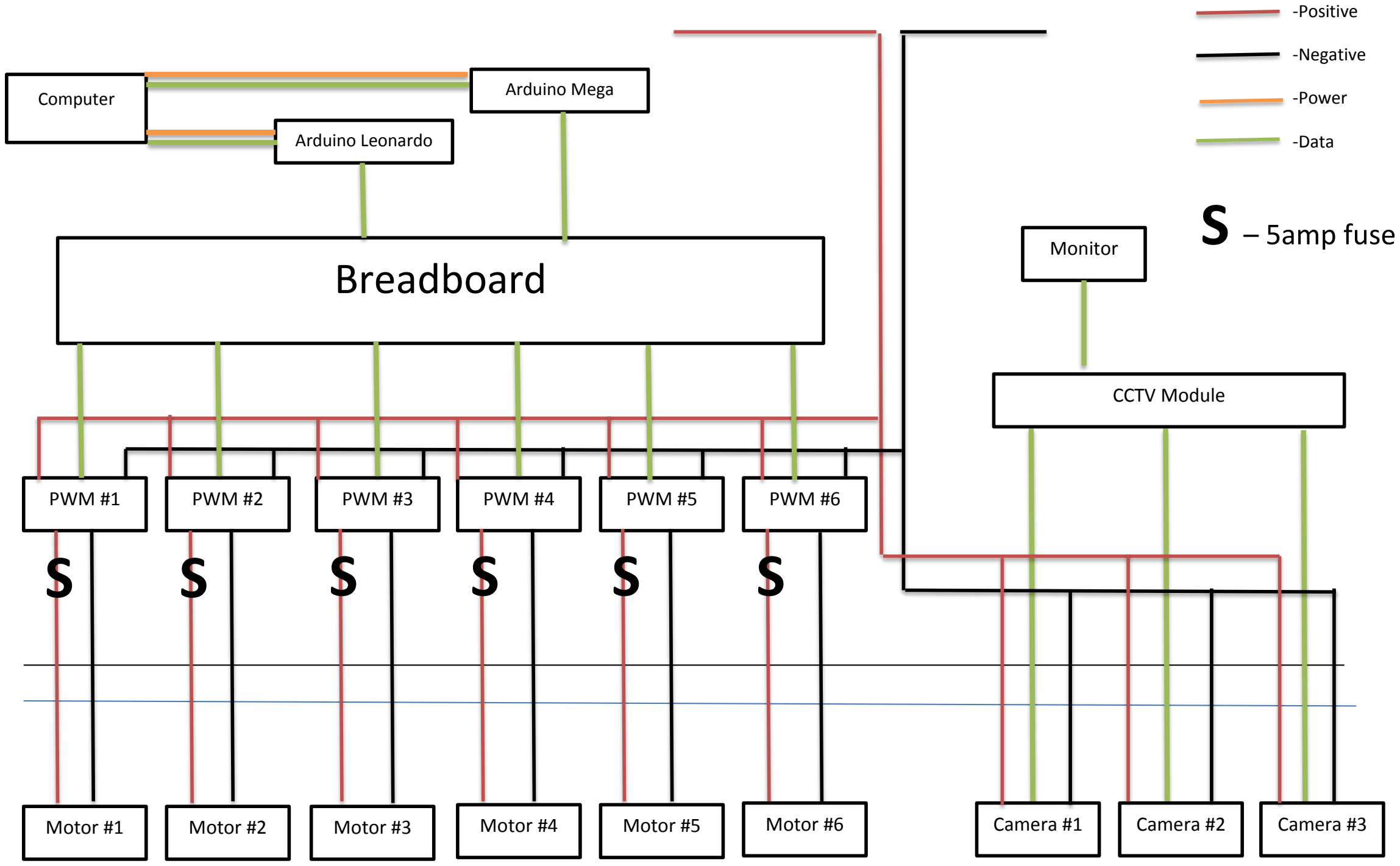
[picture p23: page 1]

PWM #1 | PWM #2 | PWM #3 | PWM #4 | PWM #5 | PWM #6

Monitor

CCTV Module

S | S | S | S | S | S
Motor #1 | Motor #2 | Motor #3 | Motor #4 | Motor #5 | Motor #6

# Breadboard

Computer | Arduino Mega

Arduino Leonardo

Camera #1 | Camera #2 | Camera #3

-Positive

-Negative

-Power

-Data

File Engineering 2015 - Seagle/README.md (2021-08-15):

## Engineering-2015-Seagle

<br>

This is the container for all the works of Seagle. Seagle is a collaborative effort of the whole AIS Engineering Club - ROV Team in 2015.

<br>

**A picture of the ROV**:

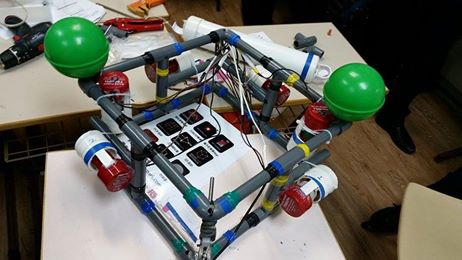
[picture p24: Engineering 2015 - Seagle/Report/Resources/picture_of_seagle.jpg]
Picture of the Seagle


<br>

**Technical Report**:

[Seagle Technical Report](Report/report.pdf)

<br>

**Company Specification Sheet**:

[Specification Sheet](Report/Resources/specification_sheet.pdf)

<br>

**ROV System Integration Diagram**:

[System integration diagram](Report/Resources/system_integrated_diagram.pdf)

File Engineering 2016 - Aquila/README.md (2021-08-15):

# Engineering-2016-Aquila-I

<br>

This is the container for all the works of Aquila. Aquila is a collaborative effort of the whole AIS Engineering Club - ROV Team in 2016.

<br>

**A picture of the ROV**:

Picture of the Aquila

<br>

**Technical Report**:

[Aquila Technical Report](Report/report.pdf)

<br>

**Poster**:

Aquila Poster

<br>

**Company Specification Sheet**:

Specification Sheet

<br>

**ROV System Integration Diagram**:

System integration diagram

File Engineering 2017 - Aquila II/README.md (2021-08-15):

## Engineering-2017-Aquila-II

<br>

This is the container for all the works of Aquila II. Aquilla II is a collaborative effort of the whole AIS Engineering Club - ROV Team in 2017.

<br>

**A picture of the ROV**:

Picture of the Aquila II

<br>

**Technical Report**:

[Aquila II Technical Report](Report/report.pdf)

<br>

**Company Specification Sheet**:

Specification Sheet

<br>

**ROV System Integration Diagram**:

System integration diagram

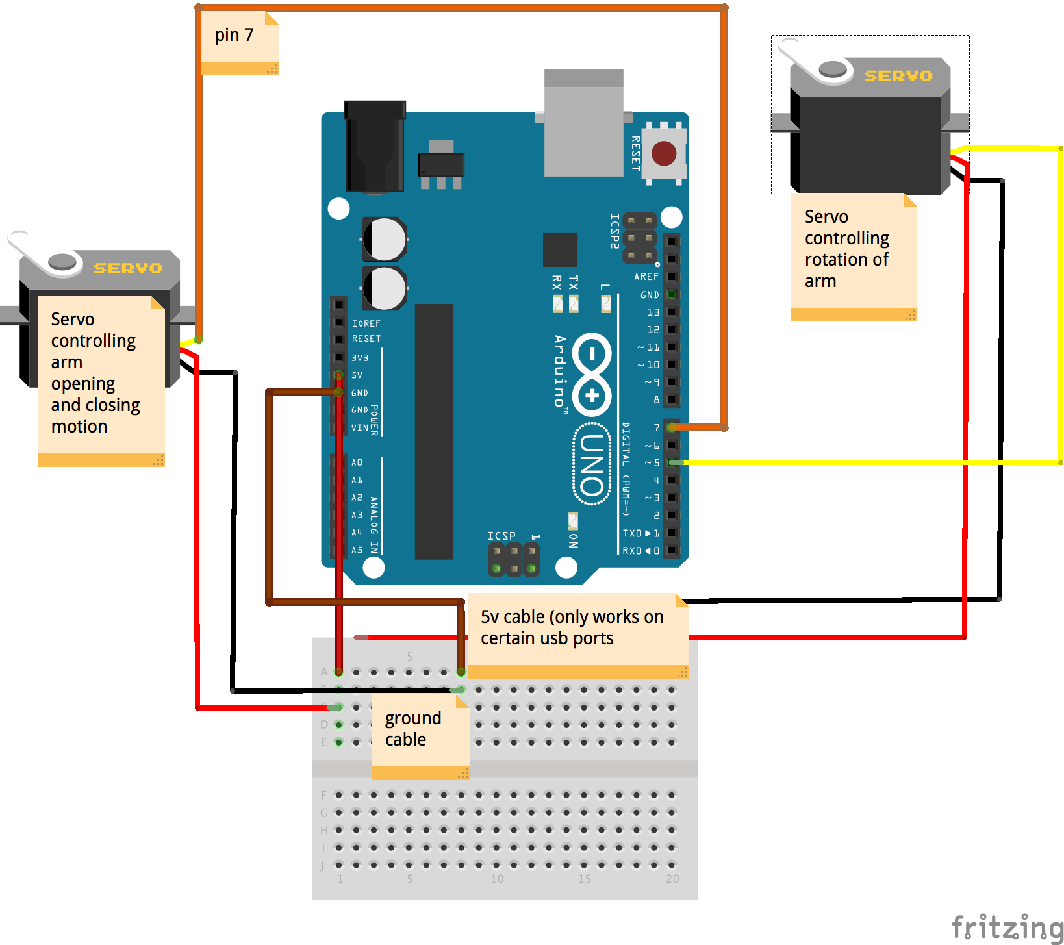
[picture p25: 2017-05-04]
Engineering 2017 - Aquila II/Electronics/Pictures/Servo Arm.png

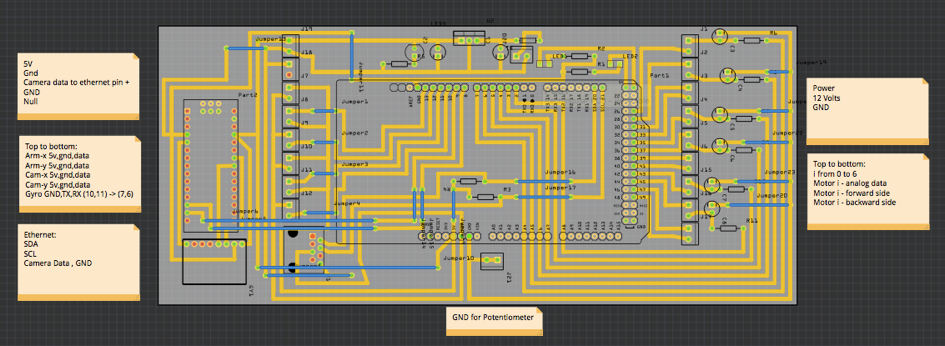
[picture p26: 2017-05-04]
Engineering 2017 - Aquila II/Electronics/Pictures/Underwater Circuit.png

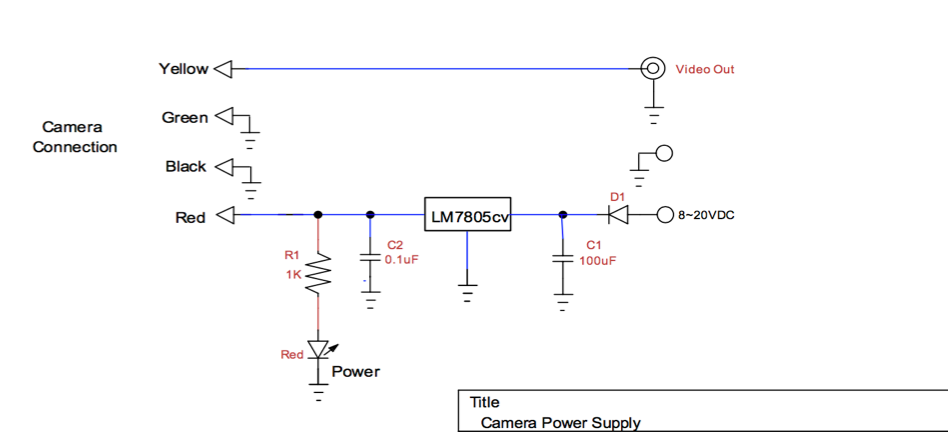
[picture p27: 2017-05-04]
Engineering 2017 - Aquila II/Electronics/Pictures/Camera Schematic.png

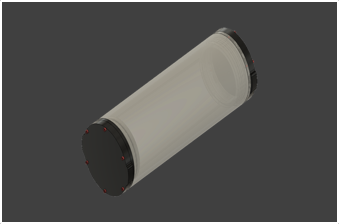
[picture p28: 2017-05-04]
Engineering 2017 - Aquila II/Report/Appendix/Section B/Figure B.3.png

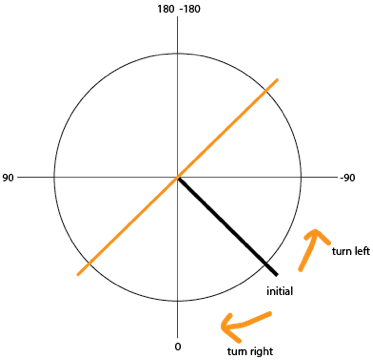
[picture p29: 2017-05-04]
Engineering 2017 - Aquila II/Report/Appendix/Section D/Figure D.4.png

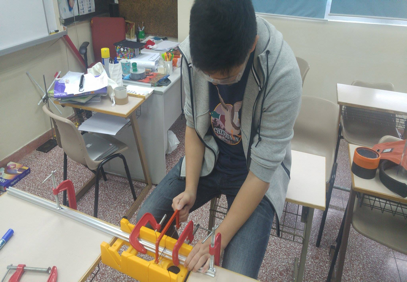
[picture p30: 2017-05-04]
Engineering 2017 - Aquila II/Report/Appendix/Section E/Figure E.1.png

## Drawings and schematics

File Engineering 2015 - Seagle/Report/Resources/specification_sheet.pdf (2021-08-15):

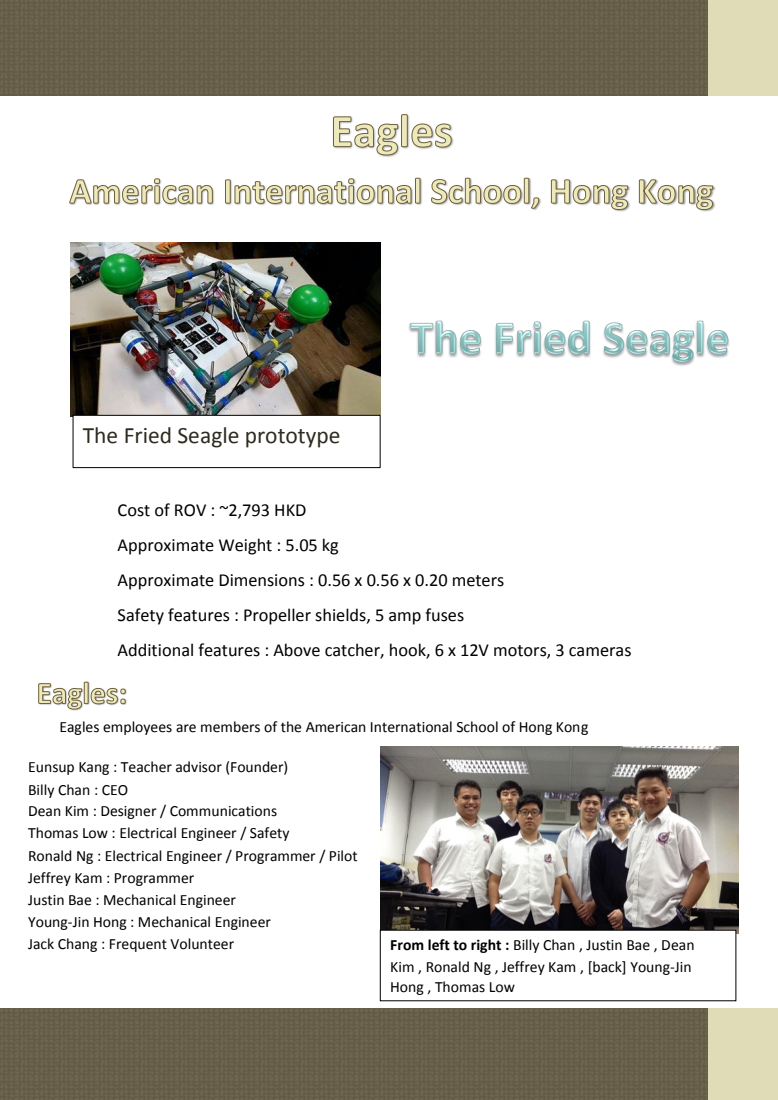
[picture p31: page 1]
asdf; Jack Chang : Frequent Volunteer; From left to right : Billy Chan , Justin Bae , Dean

The Fried Seagle prototype

Cost of ROV : ~2,793 HKD

Approximate Weight : 5.05 kg

Approximate Dimensions : 0.56 x 0.56 x 0.20 meters

Safety features : Propeller shields, 5 amp fuses

Additional features : Above catcher, hook, 6 x 12V motors, 3 cameras

Eagles employees are members of the American International School of Hong Kong

Eunsup Kang : Teacher advisor (Founder)
Billy Chan : CEO
Dean Kim : Designer / Communications
Thomas Low : Electrical Engineer / Safety
Ronald Ng : Electrical Engineer / Programmer / Pilot
Jeffrey Kam : Programmer
Justin Bae : Mechanical Engineer
Young-Jin Hong : Mechanical Engineer

Kim , Ronald Ng , Jeffrey Kam , [back] Young-Jin
Hong , Thomas Low

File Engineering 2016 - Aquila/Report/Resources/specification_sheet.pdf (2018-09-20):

# AMERICAN INTERNATIONAL SCHOOL

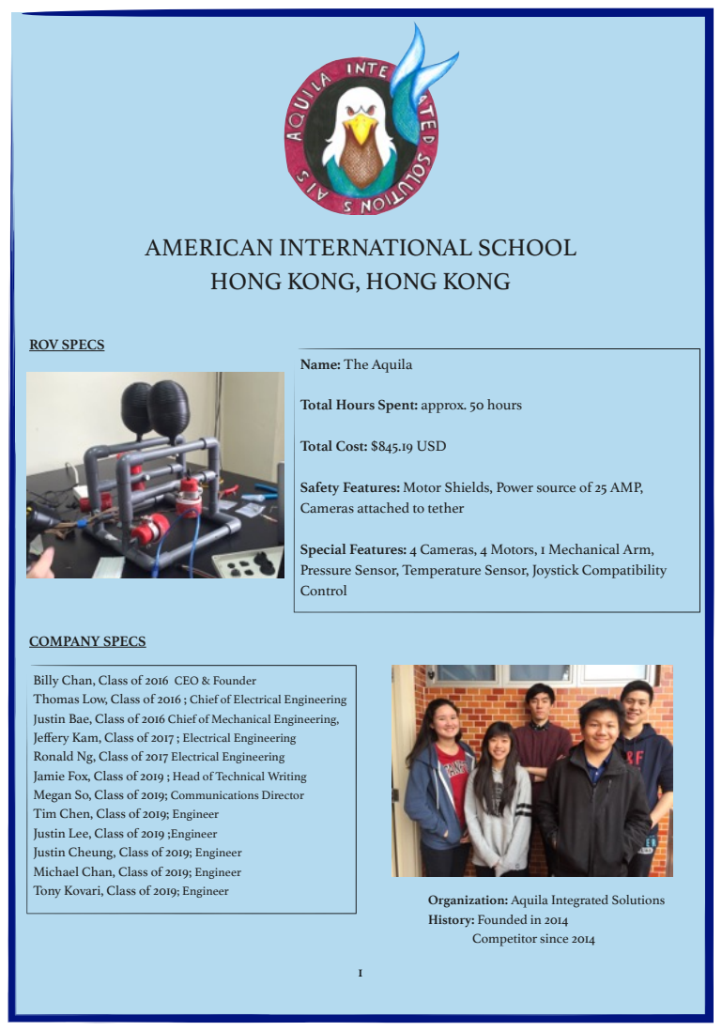
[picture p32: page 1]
ROV SPECS; COMPANY SPECS; Tony Kovari, Class of 2019; Engineer; Organization: Aquila Integrated Solutions

HONG KONG, HONG KONG

Name: The Aquila

Total Hours Spent: approx. 50 hours

Total Cost: $845.19 USD

Safety Features: Motor Shields, Power source of 25 AMP,
Cameras attached to tether

Special Features: 4 Cameras, 4 Motors, 1 Mechanical Arm,
Pressure Sensor, Temperature Sensor, Joystick Compatibility
Control

Billy Chan, Class of 2016 CEO & Founder
Thomas Low, Class of 2016 ; Chief of Electrical Engineering
Justin Bae, Class of 2016 Chief of Mechanical Engineering,
Jeffery Kam, Class of 2017 ; Electrical Engineering
Ronald Ng, Class of 2017 Electrical Engineering
Jamie Fox, Class of 2019 ; Head of Technical Writing
Megan So, Class of 2019; Communications Director
Tim Chen, Class of 2019; Engineer
Justin Lee, Class of 2019 ;Engineer
Justin Cheung, Class of 2019; Engineer
Michael Chan, Class of 2019; Engineer

History: Founded in 2014
Competitor since 2014

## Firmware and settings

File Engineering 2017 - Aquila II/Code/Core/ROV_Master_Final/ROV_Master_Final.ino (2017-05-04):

//Author: Jeffrey Kam
//Date: 10th April 2017, 3rd Janurary 2017
#include "SoftwareSerial.h"
//software serial port for mpu and main arduino communcation
#define softRX 3
#define softTX 4

#include "Wire.h"
#ifdef dobogusinclude
#include <spi4teensy3.h>
#include <SPI.h>
#endif
#include <PS3USB.h>
#include <usbhub.h>

SoftwareSerial vrSerial(softRX, softTX);
USB Usb;
PS3USB PS3(&Usb); // This will just create the instance
USBHub Hub1(&Usb); // Some dongles have a hub inside

//variable for pins
int vrSwitch = 2;

//variables for different modes
int controlMode = 0; //0 for ps3 control
int processMode = 0; //0 for initial waiting, 1 for setup, 2 for stop, 3 for play
int vrMode = 0; //0 = ps3 camera control, 1 = vr camera control
int startUpSteps = 1;

//arm angle threshold
int armMinT = 0;
int armMaxT = 180;

//arm current angle
int armAngX = (armMinT + armMaxT) / 2;
int armAngY = (armMinT + armMaxT) / 2;

//camera angle threshold
int leftCamT = 0;
int rightCamT = 180;
int upCamT = 106;
int downCamT = 180;

int vrCamX = 0;
int vrCamY = 0;

//camera current angle
int camAngX = (leftCamT + rightCamT) / 2; //90 mid
int camAngY = (upCamT + downCamT) / 2; //143 mid

//variables for limits of control and speed
int joystickThresholdMin = 35;
int joystickThresholdMax = 220;

int minSpeed = -240;
int maxSpeed = 240;
int stationarySpeed = 0;

//speed variables for motors
int lSpeed = 0;
int rSpeed = 0;
int speedZ1 = 0;
int speedZ2 = 0;
int speedZ3 = 0;
int speedZ4 = 0;
boolean zStationary = true;

//send to rov section
String compiledString = "";

void setup()
{
  Wire.begin();
  Serial.begin(115200);
  //Serial.println(1);
  #if !defined(__MIPSEL__)
    while (!Serial); // Wait for serial port to connect - used on Leonardo, Teensy and other boards with built-in USB CDC serial connection
  #endif
  if (Usb.Init() == -1) {
    while (1); //halt
  }
  vrSerial.begin(9600);
}

void loop() {
  Usb.Task();
  if (processMode == 0) {
    //wait for startup command
    if (PS3.PS3Connected || PS3.PS3NavigationConnected) {
      int tA = PS3.getAnalogButton(TRIANGLE);
      if (tA != 0) {
        processMode = 1;
      }
    }
    delay(50);
  } else if (processMode == 1) {
    startUpProcess(startUpSteps);
  } else if (processMode == 2) {
    if (PS3.PS3Connected || PS3.PS3NavigationConnected) {
      int sA = PS3.getAnalogButton(SQUARE);
      if (sA >= 100) {
        processMode = 3;
      }
    }
    delay(100);
  } else if (processMode == 3) {
    if (controlMode == 0) {
      controlModePS3();
    }
  }
  //debugMotorOutput(lSpeed, rSpeed, speedZ1, speedZ2, speedZ3, speedZ4);
  sendROVStats();
  delay(120);
}

//---Section of Main Control Code---
void controlModePS3() {
  Usb.Task();
  if (PS3.PS3Connected || PS3.PS3NavigationConnected) {
    //left right motor control
    int leftValue = PS3.getAnalogHat(LeftHatY);
    int rightValue = PS3.getAnalogHat(RightHatY);
    //up down motor control
    int L2Val = PS3.getAnalogButton(L2); //up
    int R2Val = PS3.getAnalogButton(R2); //down
    //camera movement control
    int leftVal = PS3.getAnalogButton(LEFT);
    int rightVal = PS3.getAnalogButton(RIGHT);
    int upVal = PS3.getAnalogButton(UP);
    int downVal = PS3.getAnalogButton(DOWN);

    //arm servo control
    int L1Val = PS3.getAnalogButton(L1); //open
    int R1Val = PS3.getAnalogButton(R1); //close
    boolean startVal = PS3.getButtonClick(START); //rotate left
    Serial.println(startVal);
    boolean selectVal = PS3.getButtonClick(SELECT); //rotate right
    //process mode input
    int triangleVal = PS3.getAnalogButton(TRIANGLE); //emergency stop
    int squareVal = PS3.getAnalogButton(SQUARE); //start startup
    lSpeed = planarSpeed(leftValue);
    rSpeed = planarSpeed(rightValue);
    planarMovement(lSpeed, rSpeed);
    zMovement();
    checkVRMode();
    cameraMovement(leftVal, rightVal,upVal, downVal);
    armControlX(R1Val, L1Val);
    armControlY(startVal, selectVal);
    PS3CheckMode(triangleVal, squareVal);
  }
}

//---Section of Mode Changing Code---
void PS3CheckMode(int triVal, int squVal) {
  if (squVal >= 100) {
    processMode = 2;
  } else if (triVal >= 100) {
    processMode = 1;
  }
}
//---Section of Process 1 (Start Up Process)---
void startUpProcess(int steps) {
  if (steps == 1) {
    //debugMotorOutput(maxSpeed, maxSpeed, maxSpeed, maxSpeed, maxSpeed, maxSpeed);
    lSpeed = maxSpeed;
    rSpeed = maxSpeed;
    speedZ1 = maxSpeed;
    speedZ2 = maxSpeed;
    speedZ3 = maxSpeed;
    speedZ4 = maxSpeed;    
    startUpSteps++;
    delay(3000);
  } else if (steps == 2) {
    //debugMotorOutput(stationarySpeed, stationarySpeed, stationarySpeed, stationarySpeed, stationarySpeed, stationarySpeed);
    lSpeed = stationarySpeed;
    rSpeed = stationarySpeed;
    speedZ1 = stationarySpeed;
    speedZ2 = stationarySpeed;
    speedZ3 = stationarySpeed;
    speedZ4 = stationarySpeed;
    startUpSteps++;
    delay(2000);
  } else if (steps == 3) {
    //debugMotorOutput(minSpeed,minSpeed,minSpeed, minSpeed, minSpeed, minSpeed);
    lSpeed = minSpeed;
    rSpeed = minSpeed;
    speedZ1 = minSpeed;
    speedZ2 = minSpeed;
    speedZ3 = minSpeed;
    speedZ4 = minSpeed;
    startUpSteps++;
    delay(3000);
  } else if (steps == 4) {
    //debugMotorOutput(stationarySpeed, stationarySpeed, stationarySpeed, stationarySpeed, stationarySpeed, stationarySpeed);
    lSpeed = stationarySpeed;
    rSpeed = stationarySpeed;
    speedZ1 = stationarySpeed;
    speedZ2 = stationarySpeed;
    speedZ3 = stationarySpeed;
    speedZ4 = stationarySpeed;
    processMode = 3;
    startUpSteps = 1;
    delay(500);
  }
}

//---Section of Process 2 (STOP Process)---
void stopProcess() {
  processMode = 2;
  lSpeed = stationarySpeed;
  rSpeed = stationarySpeed;
  speedZ1 = stationarySpeed;
  speedZ2 = stationarySpeed;
  speedZ3 = stationarySpeed;
  speedZ4 = stationarySpeed;
}

void resumeProcess() {
  processMode = 3;
}

//---Section of Planar Movement---
int planarSpeed(int joystickVal) {
  return map(constrain(joystickVal, joystickThresholdMin, joystickThresholdMax), joystickThresholdMax, joystickThresholdMin, minSpeed, maxSpeed);
} 

void planarMovement(int m1, int m2) {
  lSpeed = m1;
  rSpeed = m2;
}

//---Section of Vertical Movement---
void zMovement() {
  int mag = getMagnitudeZ();
  //k is the respective values for up and down magnitude
  speedZ1 = mag;
  speedZ2 = mag;
  speedZ3 = mag;
  speedZ4 = mag;
}

int getMagnitudeZ() {
  int mag = 0;
  if (PS3.getAnalogButton(L2)) {
    mag = map(PS3.getAnalogButton(L2), 0, 255, stationarySpeed, minSpeed);
  } else if (PS3.getAnalogButton(R2)) {
    mag = map(PS3.getAnalogButton(R2), 0, 255, stationarySpeed, maxSpeed);
  }
  if (mag == stationarySpeed) {
    zStationary = true;
  } else {
    zStationary = false;
  }
  return mag;
}

//---Section of Camera Control---
void checkVRMode(){
  if(digitalRead(vrSwitch) == LOW){
    if(vrMode == 1){
      camAngX = (leftCamT + rightCamT) / 2; //90 mid
      camAngY = (upCamT + downCamT) / 2; //143 mid
    }
    vrMode = 0;
  }else{
    vrMode = 1;
  }
}

void retrieveGyroData(){
  String tempS = "";
  String a1 = "";
  String a2 = "";
  char buf1[4];
  char buf2[4];
  char c;
  boolean t = false;
  while(vrSerial.available()){
    if(c != '?'){
      c = vrSerial.read();
      tempS += c;
    }else{
      if(tempS.length()==6){
        a1 = tempS.substring(0,3);
        a2 = tempS.substring(3,6);
        a1.toCharArray(buf1, 4);
        vrCamX = atoi(buf1);
        vrCamX -= 100;
        a2.toCharArray(buf2, 4);
        vrCamY = atoi(buf2);
        vrCamY -= 100;
        break;
      }else{
        break;
      }
    }
  }
}

void cameraMovement(int lV, int rV, int uV, int dV){
  if(vrMode == 0){
    cameraControlX(lV, rV);
    cameraControlY(uV, dV);
  }else{
    //steven's code
    camAngX = 0;//some vr mapped value
    camAngY = 0;//some vr mapped value
  }
}

void cameraControlX(int lV, int rV) {
  if (lV >= 50) {
    if (inRange(camAngX, leftCamT, rightCamT)) {
      camAngX += 1;
    }
  } else if (rV >= 50) {
    if (inRange(camAngX, leftCamT, rightCamT)) {
      camAngX -= 1;
    }
  }
}

void cameraControlY(int uV, int dV) {
  if (uV >= 50) {
    if (inRange(camAngY, downCamT, upCamT)) {
      camAngY += 1;
    }
  }else if (dV >= 50) {
    if (inRange(camAngY, downCamT, upCamT)) {
      camAngY -= 1;
    }
  }
}

//---Section of Arm Control---
void armControlX(int openVal, int closeVal) {
  if (openVal >= 50) {
    if (inRange(armAngX, armMinT, armMaxT)) {
      armAngX += 1;
    }
  } else if (closeVal >= 50) {
    if (inRange(armAngX, armMinT, armMaxT)) {
      armAngX -= 1;
    }
  }
}

void armControlY(boolean openVal, boolean closeVal) {
  if (openVal) {
    armAngY += 1;
  } else if (closeVal) {
    armAngY -= 1;
  }
}
//---Section of Miscellaneous Functions---
bool inRange(double val, int minimum, int maximum) {
  return ((minimum < val) && (val < maximum));
}

int transformSpeedTo100(int val) {
  if(val == 0){
    return 0;
  }
  if(inRange(map(val, minSpeed, maxSpeed, -100, 100),-10,10)){
    return 0;
  }
  return map(val, minSpeed, maxSpeed, -100, 100);
}

//---Section of Sending ROV Status To Processing---
void sendROVStats() {
  //send current status to Processing
  //compile stats
  compiledString = "";
  compiledString += String(processMode);
  compiledString += ",";
  //arm angle
  compiledString += String(armAngX);
  compiledString += ",";
  compiledString += String(armAngY);
  compiledString += ",";
  //camera angle
  compiledString += String(camAngX);
  compiledString += ",";
  compiledString += String(camAngY);
  compiledString += ",";
  //speed stats
  compiledString += String(lSpeed);
  compiledString += ",";
  compiledString += String(rSpeed);
  compiledString += ",";
  compiledString += String(speedZ1);
  compiledString += ",!";

  Serial.println(compiledString);
  char charA[compiledString.length()];
  
  for(int i=0; i<compiledString.length(); i++){
    charA[i] = compiledString.charAt(i);
  }
  //Serial.println(compiledString.length());
  Wire.beginTransmission(9);
  Wire.write(charA,compiledString.length());
  Wire.endTransmission();    // stop transmitting
}

void debugMotorOutput(int spdRaw1, int spdRaw2, int spdRaw3, int spdRaw4, int spdRaw5, int spdRaw6) {
  //state 1 is all, 2 is vertical, 3 is planar
  String spd1 = String(transformSpeedTo100(spdRaw1));
  String spd2 = String(transformSpeedTo100(spdRaw2));
  String spd3 = String(transformSpeedTo100(spdRaw3));
  String spd4 = String(transformSpeedTo100(spdRaw4));
  String spd5 = String(transformSpeedTo100(spdRaw5));
  String spd6 = String(transformSpeedTo100(spdRaw6));
  Serial.println("Left Planar Motor : " + spd1);
  Serial.println("Right Planar Motor : " + spd2);
  Serial.println("Vertical Motor 1: " + spd3);
  Serial.println("Vertical Motor 2: " + spd4);
  Serial.println("Vertical Motor 3: " + spd5);
  Serial.println("Vertical Motor 4: " + spd6);
}

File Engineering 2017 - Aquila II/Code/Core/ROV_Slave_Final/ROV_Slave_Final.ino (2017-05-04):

//Author: Jeffrey Kam
//Date: 10th April 2017
#include "Wire.h"
#include "Servo.h"
#include "SoftwareSerial.h"
#include "PID_v1.h"

Servo cameraServoX,cameraServoY,armServoX,armServoY;
int cSA[11]; //processmode, camX, camY, armX, armY, leftSpd, rightSpd, z1Spd, z2Spd, z3Spd, z4Spd

//motor num: 0 = left horizontal, 1 = right horizontal, 2 = top left, 3 = top right, 4 = bottom left, 5 = bottom right 
int motorSpeedPins[6] = {7,6,5,4,3,2};
int motorDPins[6] = {27,31,35,39,43,47};
int cameraServos[2] = {11,10};
int armServos[2] = {13,12};

int prevMotorSpeed[6] = {0,0,0,0,0,0};

void setup() {
  Wire.begin(9); 
  Wire.onReceive(receiveEvent);
  Serial.begin(115200);
  cameraServoX.attach(cameraServos[0]);
  cameraServoY.attach(cameraServos[1]);
  armServoX.attach(armServos[0]);
  armServoY.attach(armServos[1]);
}

void loop() {

}

void receiveEvent(int bytes) {
  String compiledString = "";
  char c;
  c = Wire.read();
  while(Wire.available()){
    if(c == "!"){
      break;
    }else{
      compiledString += c;
      c = Wire.read();    // read one character from the I2C
    }
  }
  parseData(compiledString);
  debug();
  coreAlgorithm();
}

void parseData(String s){
  String tempS[8];
  int k = 0;
  for(int i=0; i<8;i++){
    while(s.charAt(k) != ','){
      tempS[i] += s.charAt(k);
      k++;
    }
    k++;
  }
  for(int j=0; j<8; j++){
    char buf[4];
    tempS[j].toCharArray(buf, 4);
    if(j == 7){
      int tempI = atoi(buf);
      cSA[j] = tempI;
      for(int k=j+1; k<=j+3; k++){
        cSA[k] = tempI;
      }
    }else{
      cSA[j] = atoi(buf);
    }
  }
}

void coreAlgorithm(){
  planarMovement();
  verticalMovement();
  cameraMovement();
  armMovement();
}

void planarMovement() {
  runMotor(0,cSA[5]);
  runMotor(1,cSA[6]);
}

void verticalMovement(){
  if(checkZStationary()){  
    runMotor(2,cSA[7]);
    runMotor(3,cSA[8]);
    runMotor(4,cSA[9]);
    runMotor(5,cSA[10]); 
  }else{
    runMotor(2,cSA[7]);
    runMotor(3,cSA[8]);
    runMotor(4,cSA[9]);
    runMotor(5,cSA[10]);  
  }
}

boolean checkZStationary(){
  if(cSA[6] == 0){
    return true;
  }
  return false;
}

void cameraMovement(){
  cameraServoX.write(cSA[1]);
  cameraServoY.write(cSA[2]);
}

void armMovement(){
  armServoX.write(cSA[3]);
  armServoY.write(cSA[4]);
}

void directionCheck(int motorNum, int motorSpeed){
  int tempSpeed = motorSpeed;
  if(numberProperty(prevMotorSpeed[motorNum]) == 0){
  }else if(numberProperty(prevMotorSpeed[motorNum]) == 1){
    if(numberProperty(motorSpeed) == 2){
      tempSpeed = 0;
    }
  }else if(numberProperty(prevMotorSpeed[motorNum]) == 2){
    if(numberProperty(motorSpeed) == 1){
      tempSpeed = 0;
    }
  }
  prevMotorSpeed[motorNum] = tempSpeed;
  runMotor(motorNum, tempSpeed);
}

void runMotor(int motorNum, int motorSpeed){
  if(motorNum == 0 || motorNum == 1){
    if(motorSpeed >= 20 && motorSpeed <= 255){
      digitalWrite(motorDPins[motorNum], HIGH);
      digitalWrite(motorDPins[motorNum]+2, LOW);
      analogWrite(motorSpeedPins[motorNum], mappedSpeed(motorSpeed));
    }else if(motorSpeed <= 20 && motorSpeed >= -255){
      digitalWrite(motorDPins[motorNum], LOW);
      digitalWrite(motorDPins[motorNum]+2, HIGH);
      analogWrite(motorSpeedPins[motorNum], mappedSpeed(motorSpeed));
    }else{
      digitalWrite(motorDPins[motorNum], LOW);
      digitalWrite(motorDPins[motorNum]+2, LOW);
      analogWrite(motorSpeedPins[motorNum], 0);
    }
  }else{
    if(motorSpeed >= 20 && motorSpeed <= 255){
      digitalWrite(motorDPins[motorNum], HIGH);
      analogWrite(motorSpeedPins[motorNum], mappedSpeed(motorSpeed));
    }else if(motorSpeed <= 20 && motorSpeed >= -255){
      digitalWrite(motorDPins[motorNum], LOW);
      analogWrite(motorSpeedPins[motorNum], mappedSpeed(motorSpeed));
    }else{
      digitalWrite(motorDPins[motorNum], LOW);
      analogWrite(motorSpeedPins[motorNum], 0);
    }
  }
}

int mappedSpeed(int motorSpeed){
  return map(abs(motorSpeed),0,255,255,0);
}

int numberProperty(int n){
  if(n == 0){
    return 0;
  }else if(n > 0){
    return 1;
  }else{
    return 2;
  }
}

void debug(){
  for(int i=0; i<11; i++){
    Serial.print(cSA[i]);
    Serial.print(",");
  }
  Serial.print("\n");
}
